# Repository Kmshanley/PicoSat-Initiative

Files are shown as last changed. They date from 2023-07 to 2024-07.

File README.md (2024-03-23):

# PicoSat-Initiative
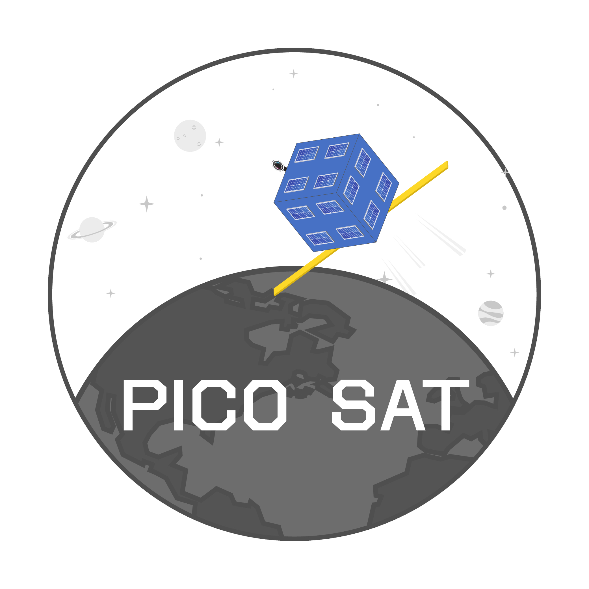
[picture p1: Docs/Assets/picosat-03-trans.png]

The Wentworth Picosat initiative is a group at Wentworth Institute of technology dedicated to making a pocket cube satellite capable of earth observation from LEO.

The pocket cube standard requires satellites to be 5x5x5cm and under 250 grams. Upon completion of this Wentworth PicoSat it will become one of the smallest satellites capable of high resolution imagery from LEO.

* **Homepage:** <https://picosat.notion.site>
* **Communication:** <https://discord.gg/C9kFq642a>

Organization
------------------------
This repository is divided into two primary sections:
### Test
> Contains all firmware related to testing boards or individual components.
### Flight
> Contains the development for the main flight firmware that will be deployed in space.

Getting Started
------------------------
The easiest way to get started is by using the Stm32CubeIDE.

Downloadable here: https://www.st.com/en/development-tools/stm32cubeide.html

From here you should be able to import the various project files (.ioc) and CubeIDE will handle setup, build tools, and compilation.

High Level Overview
------------------------
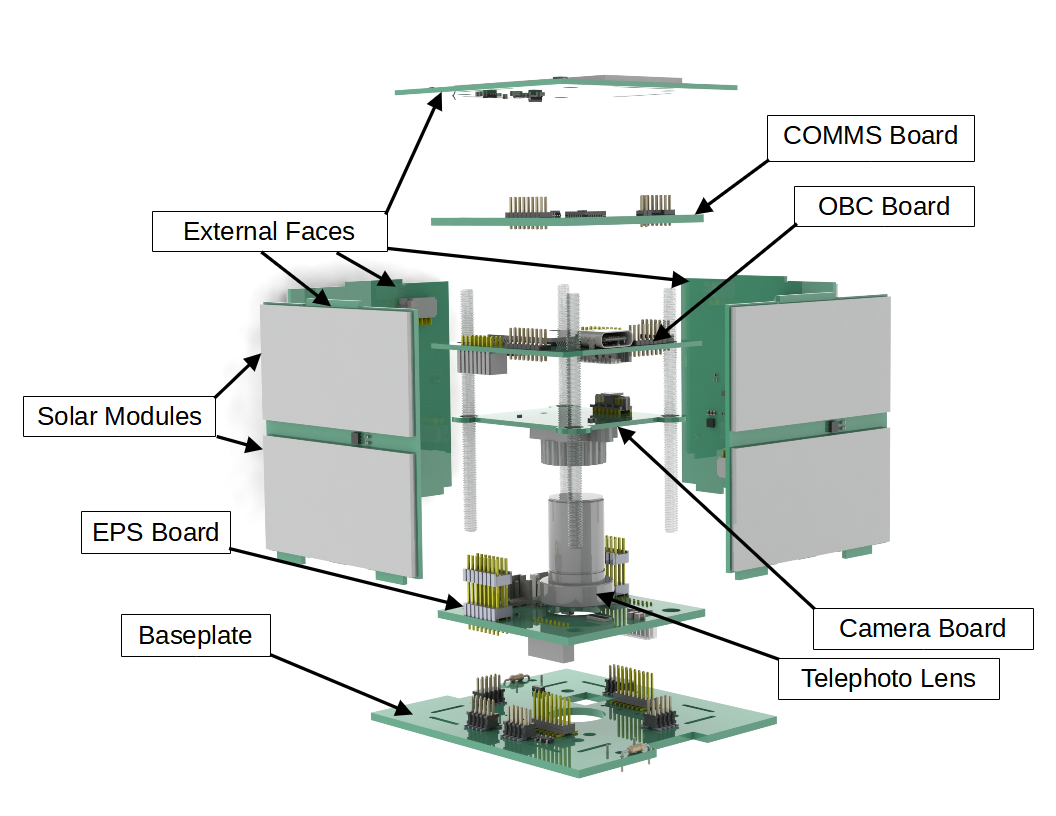
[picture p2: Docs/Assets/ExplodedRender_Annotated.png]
Exploded and Annotated Render of the Satellite's Internal Stack


The Satellite is composed of several **subsystems**:

* Onboard Computer System (OBC)
    * Responsible for handling commands from the ground station
    * Running ADCS algorithms
    * Commanding the image sensor to take pictures
        * Compressing and Storing these pictures until downlink
    * Gathering telemetry from sensors
        * Feeding telemetry to the appropriate subsystem
            * I.e. LUX sensor data to ADCS
    * Managing Satellite Energy consumption
        * Monitoring battery health and determining wakeup periods
* Electrical Power System (EPS)
    * Responsible for generating, storing, and regulating electrical power
* Communications (COMMS)
    * Responsible for uplink and downlink to ground station 
* Attitude Control and determination (ADCS)
    * Responsible for determining the attitude (rotation) of the satellite
    * Responsible for executing rotational maneuvers

Hardware Overview
------------------------
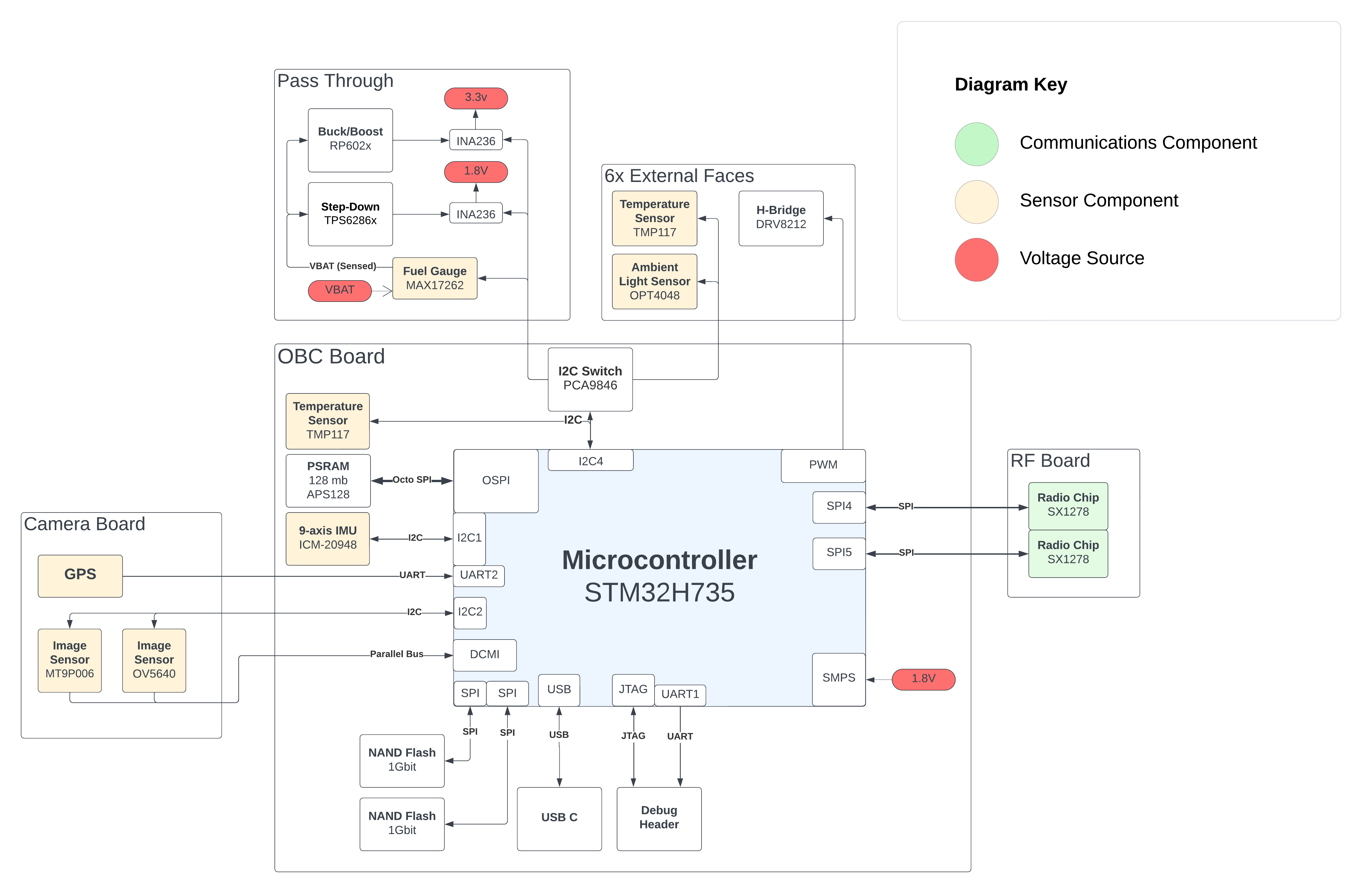
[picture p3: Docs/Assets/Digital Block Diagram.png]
System diagram of all satellite components


Contact
------------------------
You can join our discord with the link above or contact us directly via email:

OBC Team Lead (Kieran Shanley): <kmshanley01@gmail.com>

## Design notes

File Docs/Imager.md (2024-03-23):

# Imager

The Satellite's primary goal is to capture high resolution photos of the surface of the earth.

In order to accomplish this, the satellite is equipped with two cameras.

1. OV5640 image sensor (Wide angle camera)
    * Connected to the camera board via ribbon cable
    * 5 MP (2592 H x 1944 V)
    * 250 m/pix GSD
    * 67 degree FOV
    * Optical Format 1/4"
2. MT9P006 image sensor (telephoto)
    * Directedly soldered to camera board
    * 5 MP (2592 H x 1944 V)
    * 50 m/pix GSD
    * 12 degree FOV
    * Optical Format 1/2.5"

Both cameras have a I/O line dedicated to shutting down the sensor. These two lines will allow us have the image sensors share data busses; by only having one sensors active at a time. Each sensor is connected to two data busses: DCMI (parallel) and I2C. The I2C bus is used to command and configure the sensor. The DCMI bus is used to transfer image data.

The DCMI bus is accessible via a DMA (direct memory access) master. This allows data to be transferred out of the DCMI bus hardware to a memory location without using the CPU.

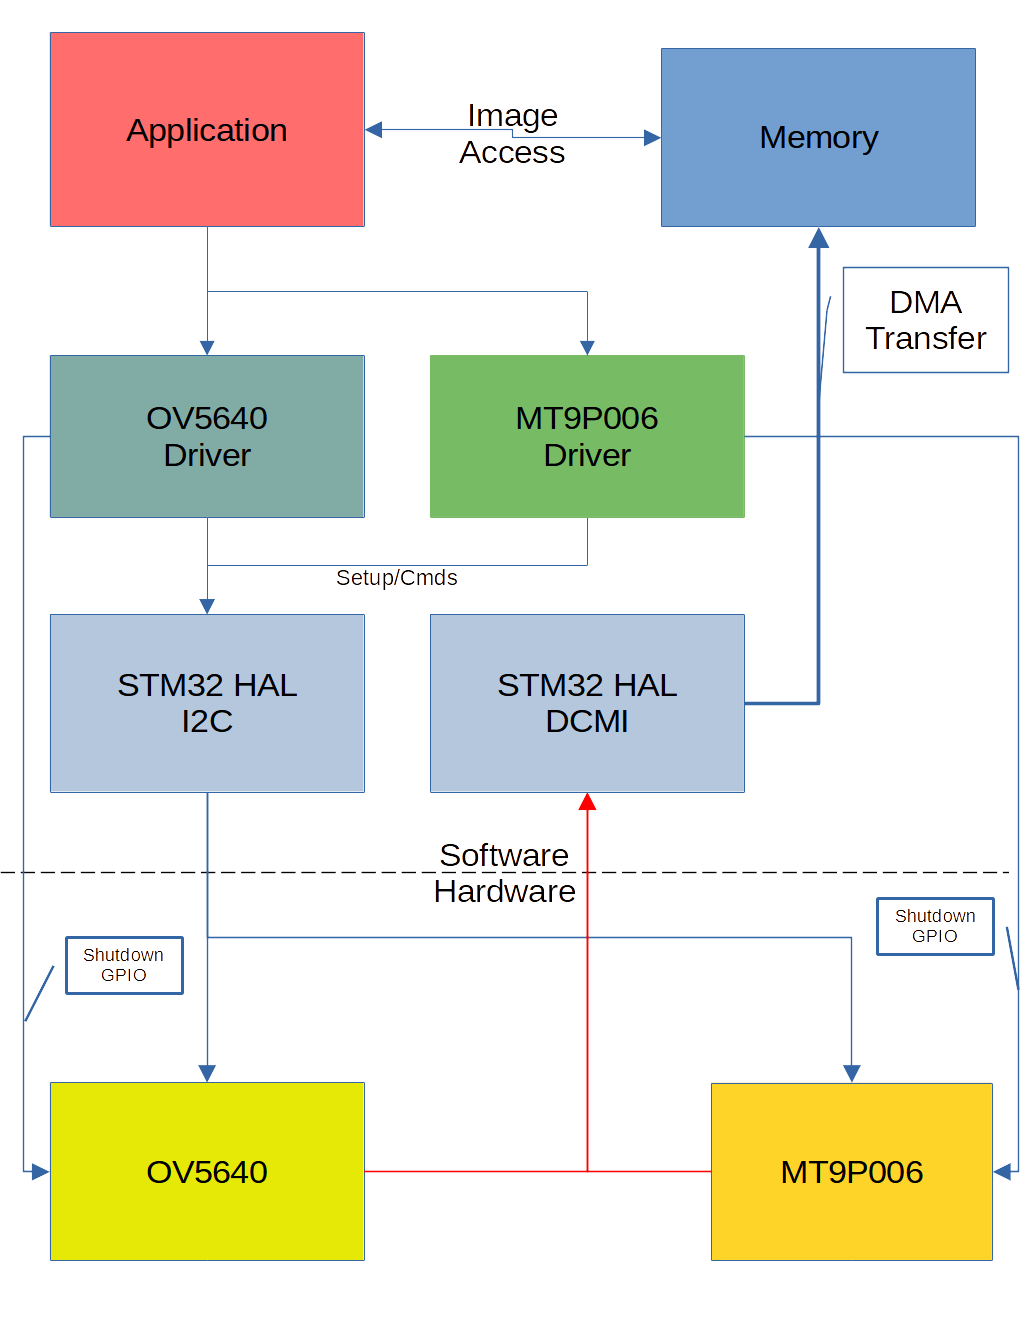
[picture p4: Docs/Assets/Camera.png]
Diagram of the Camera Software Architecture


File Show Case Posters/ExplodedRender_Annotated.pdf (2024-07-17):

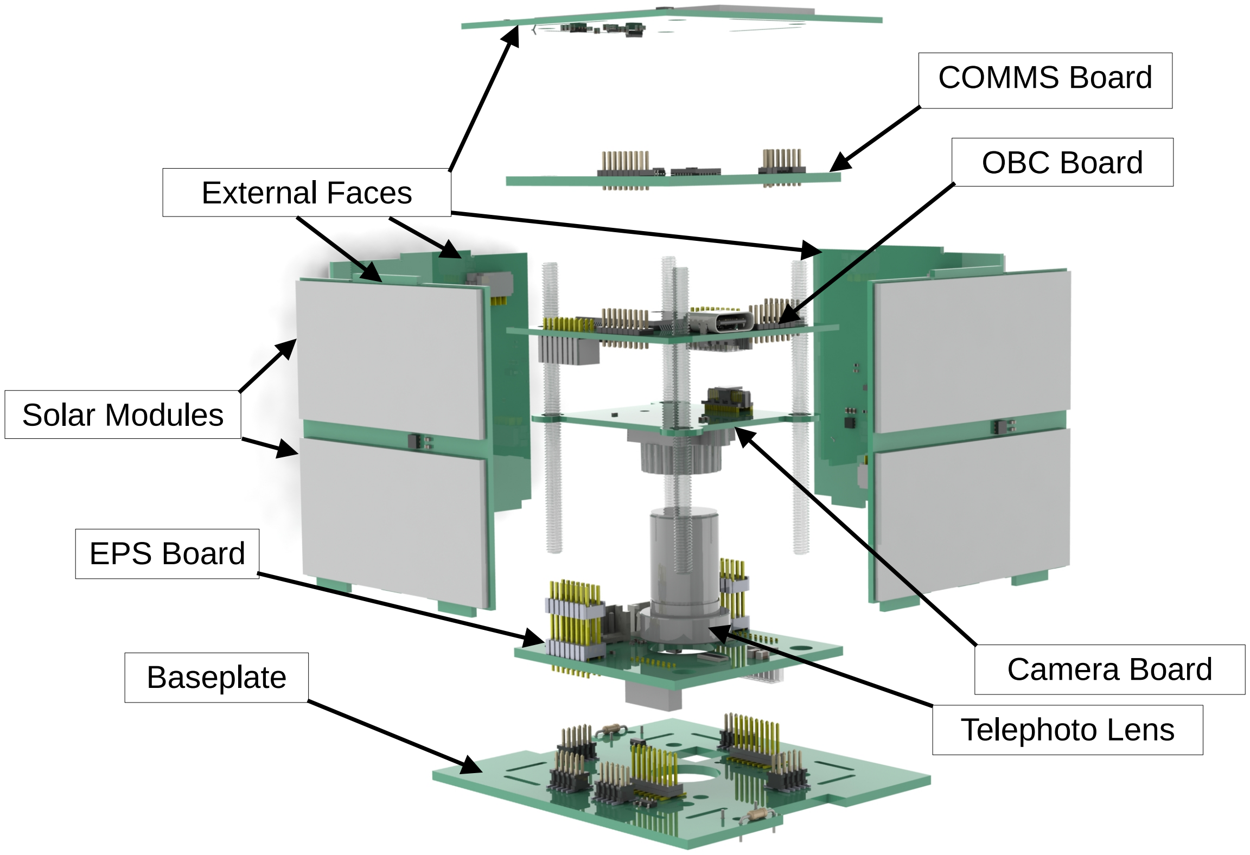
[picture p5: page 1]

COMMS Board

OBC Board

Camera Board

EPS Board

Baseplate
Telephoto Lens

External Faces

Solar Modules

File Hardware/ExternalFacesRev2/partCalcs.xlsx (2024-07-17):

SPV1040 Inductor
Vout | 4.2
Vmpp | 3.35
Pmax (mW) | 368
Duty Cycle | 0.2023809524
Switching Frequency | 100000 |  |  | 1.5e-08
CM mode inductance | 6.245267865e-09 |  | 30% | -30%
Lx | 9.91873805e-06 |  | 1.95e-08 | 1.05e-08
9e-06
Voc | 4.15
Imax | 0.1172
Output voltage partitioning
Vout Max | 4.2
Resistor ratio | 2.3600
 | R1 | R2
Slected Resistors | 1000000 | 420000
Vout Real | 4.226190476

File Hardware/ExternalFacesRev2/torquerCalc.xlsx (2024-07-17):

Total Resistance | Coil Resistance (Ohms) | Area Sum (m^2) | Number of Coils | Voltage | Amps | Magnetic Dipole (A-m^2) | Watts | Watt per dipole | Lat | Long | Altitude (km) | Description | North Comp (nT) | East/West Comp (nT) | Vertical Comp (nT) | Total |  | Roll (N * m) | Pitch (N * m) | Yaw (N * m) | Roll (rad/s^2) | Pitch (rad/s^2) | Yaw (rad/s^2) | Roll (deg /s^2) | Pitch (deg /s^2) | Yaw (deg /s^2)
150 | 75 | 0.1356 | 2 | 3.7 | 0.02466666667 | 0.0033448 | 0.09126666667 | 27.28613569 | 42° 21' 31" N | 71° 3' 24" W | 700 | LEO over bosto | 1.44234e-05 | -3.1452e-06 | 3.39189e-05 | 3.69914e-05 | 0 | -5.460501954e-07 | 0 | 2.321979896e-07 | -0.005242081876 | 0 | 0.0022291007 | -0.3003491673 | 0 | 0.1277180622
100 | 50 | 0.145 | 2 | 3.7 | 0.037 | 0.005365 | 0.1369 | 25.51724138 |  | Dipole vector: |  |  | 0 | 0.0160987 | 0 |  | 1e-09
100 | 50 | 0.145 | 2 | 10 | 0.1 | 0.0145 | 1 | 68.96551724
100 | 25 | 0.29 | 4 | 3.7 | 0.037 | 0.01073 | 0.1369 | 12.75862069 |  |  |  |  |  |  |  |  | Mass of Sat
100 | 16.66666667 | 0.4351 | 6 | 3.7 | 0.037 | 0.0160987 | 0.1369 | 8.503792232 |  |  |  |  |  |  |  |  | 0.25
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

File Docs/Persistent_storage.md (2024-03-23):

# Persistent Storage

OBC flight is equipped with 2x 1Gbit W25N01GW Winbond QSPI NAND flash chips.
These chips are 1Gbit, or 128M-byte in size. They are connected to the STM32H7 primary microcontroller via QSPI.
However, from the perspective of the STM32H7 these two chips are connected to a OCTOSPI interface, which is then split into two QSPI interfaces.

One issue with these NAND chips is that they have a 128K-Byte block size. Which means that the **minimum** amount of data that can be erased in one operation is 128K-bytes. NAND flash may also ship with *bad blocks* (blocks that cannot be read from or written to), or develop them in there lifespan. NAND flash also experiences significant wear on writes/erases (W25N01 is rated for 10,000 cycles), necessitating the use of special data organization to ensure *wear leveling*.

Luckily, there are filesystems designed for this exact application.
The filesystem we chose for our satellite is **YAFFS** (<https://yaffs.net/>).
YAFFS is designed to directly interact with and handle NAND flash. This will allow us to abstract away complex NAND file handing and be able to simply access files from a *POSIX-like interface*. 

Yaffs also supplies a special wrapped for RTOS's, called *Yaffs Direct Interface*. We will be using this wrapped to integrate YAFFS with FREERTOS.

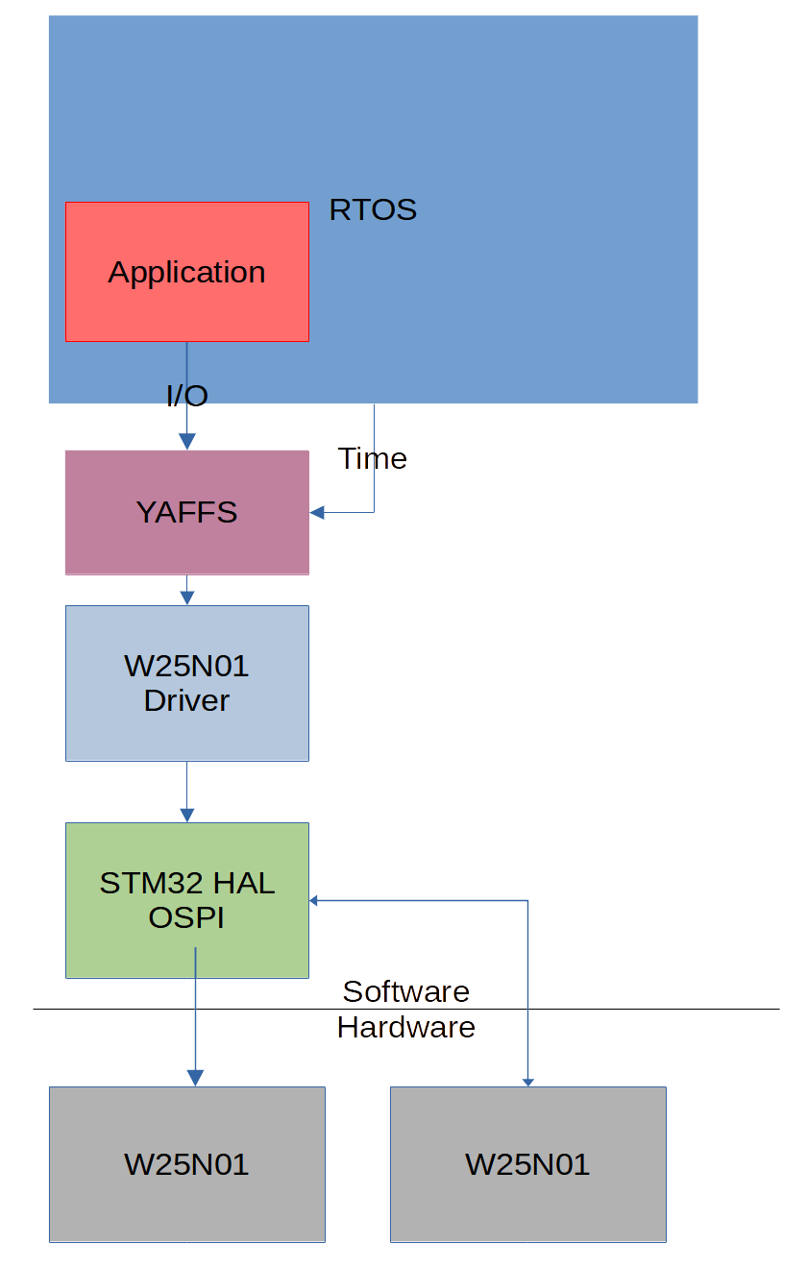
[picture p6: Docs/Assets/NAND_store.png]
Diagram of the Storage software Architecture


# Usage
* Pictures
* Ephemeris Data
* Logging
    * A max file size will be allocated
        * Once this size is reached, the oldest logs will be overwritten
* Firmware images 
    * Images uploaded from the ground station will first be loaded into NAND

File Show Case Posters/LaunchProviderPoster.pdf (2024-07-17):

# How to get to LEO: Launch Provider

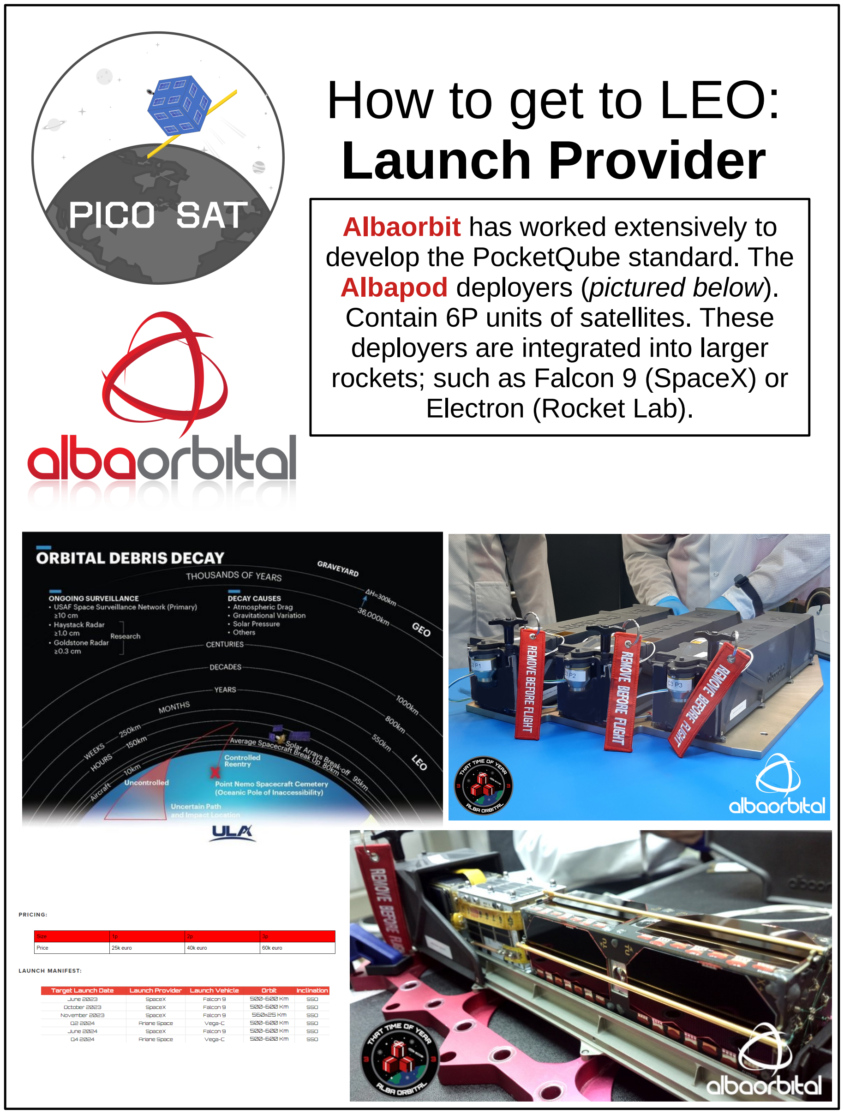
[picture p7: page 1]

Albaorbit has worked extensively to develop the PocketQube standard. The Albapod deployers (pictured below). Contain 6P units of satellites. These deployers are integrated into larger rockets; such as Falcon 9 (SpaceX) or Electron (Rocket Lab).

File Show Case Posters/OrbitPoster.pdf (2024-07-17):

# Destination: Low Earth Sun

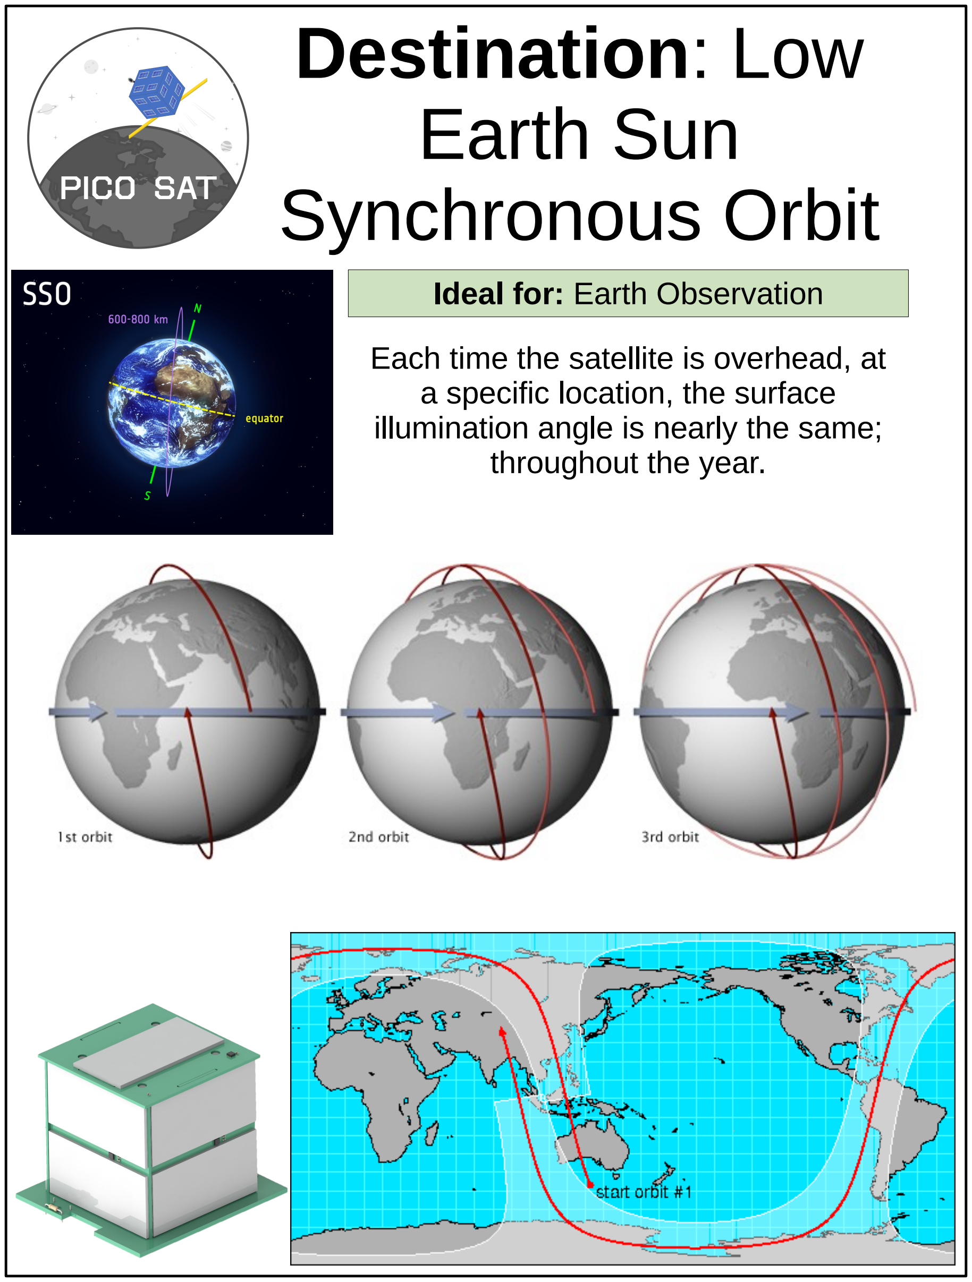
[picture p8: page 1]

# Synchronous Orbit

Each time the satellite is overhead, at a specific location, the surface illumination angle is nearly the same; throughout the year.

Ideal for: Earth Observation

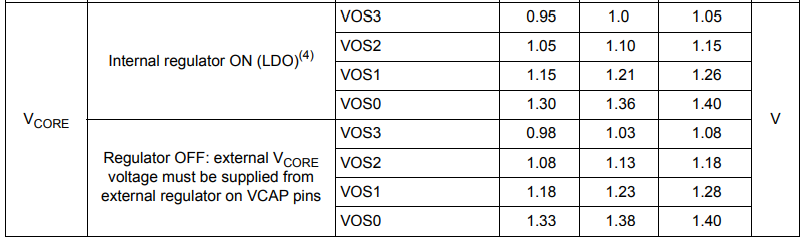
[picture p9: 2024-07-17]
Hardware/OBC-Flight_Rev0/VcoreSupplyOpCond.PNG

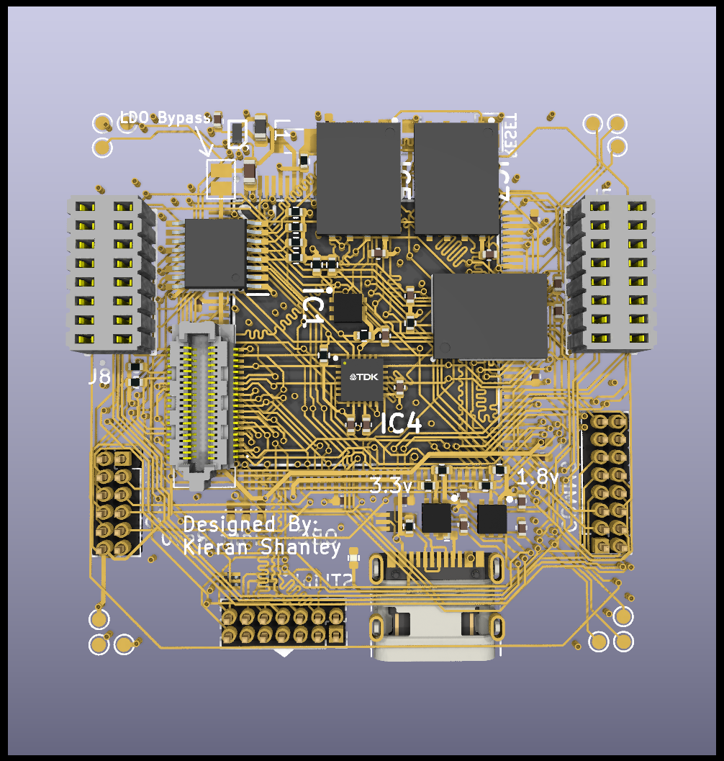
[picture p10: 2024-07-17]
Hardware/OBC-Flight_Rev0/OBC-Flight_SeeThroughBack.png

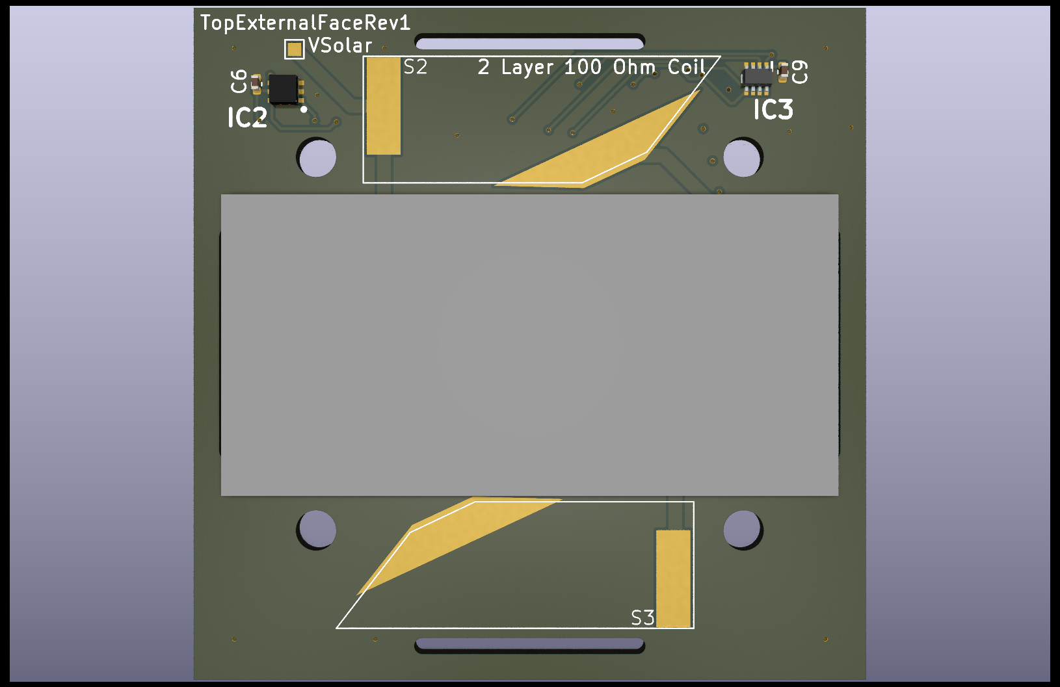
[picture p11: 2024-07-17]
Hardware/TopExternalFaceRev1/TopExternalFaceRev1_Top.png

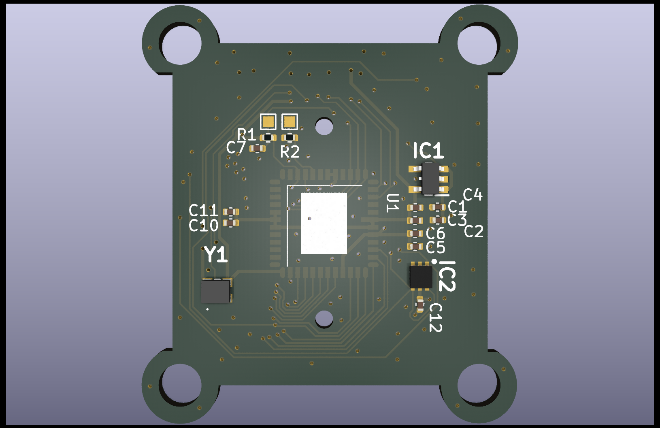
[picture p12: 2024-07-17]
Hardware/CameraBoard_Rev0/CameraBoard_Bottom.png

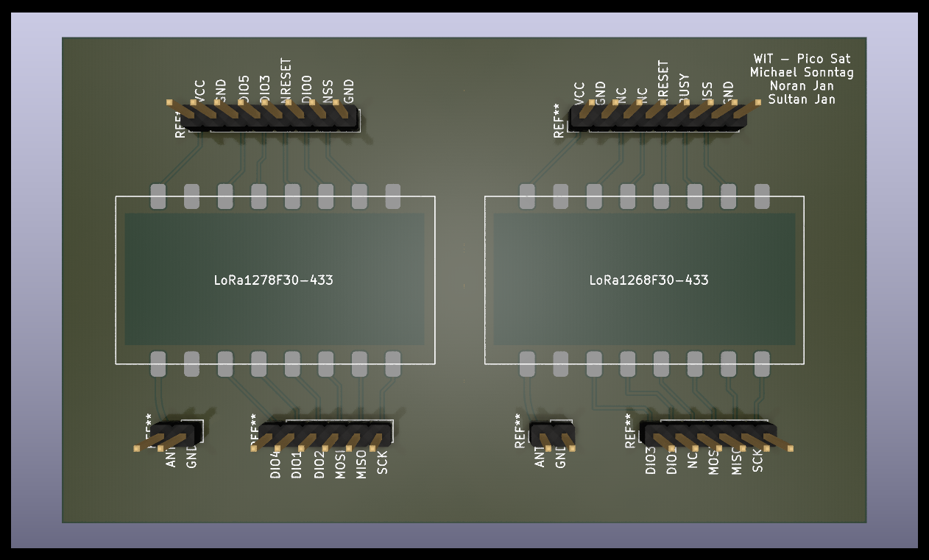
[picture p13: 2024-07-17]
Hardware/G-NiceRF Breakout Board/G-NiceRF Breakout Board.png

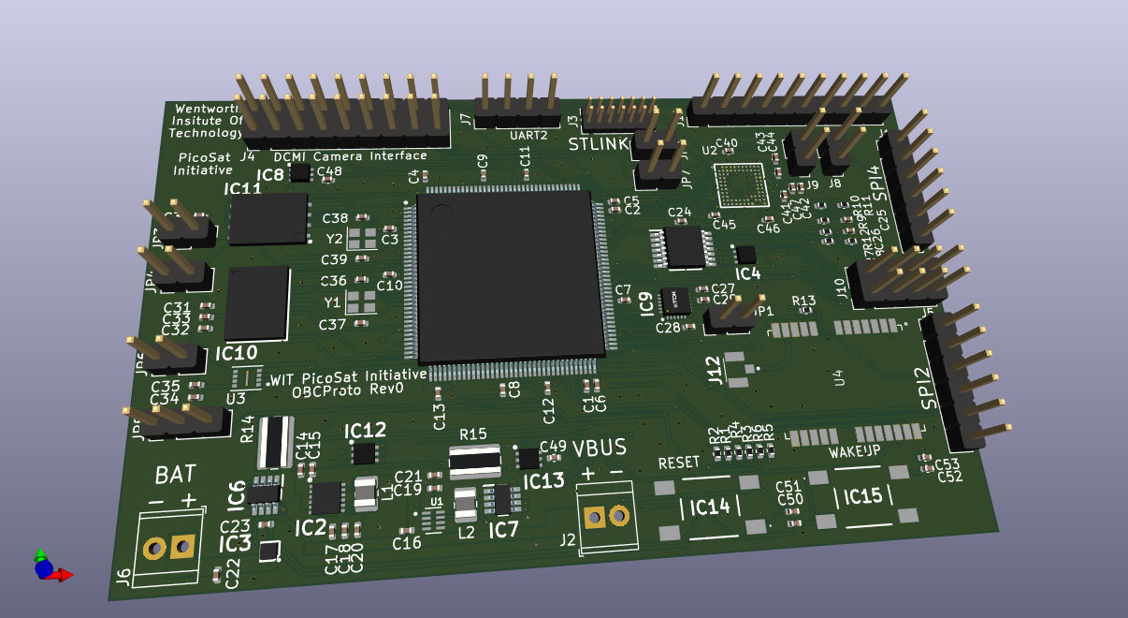
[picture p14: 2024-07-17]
Hardware/OBCProto/OBCProto.png

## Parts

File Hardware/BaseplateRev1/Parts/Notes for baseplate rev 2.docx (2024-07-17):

Re route everything

Move caps away from screw hole

Route rf signal to both poles of dipole

Pick and implement different transistors

Move kill switches back to appropriate position and make them even

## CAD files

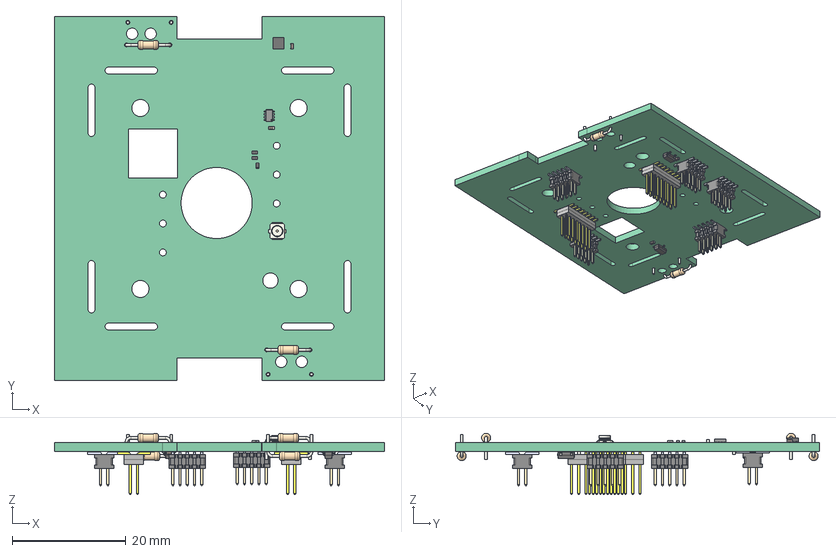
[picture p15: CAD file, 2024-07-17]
Hardware/BaseplateRev1/BaseplateRev1.step
58.0 x 64.0 x 10.8 mm
Pcb_3d0
REFinduc_R_0402_1005Metric_394f7394ac2b x 3
R1_R_Axial_DIN0204_L36mm_D16mm_P762mm_Horizontal_5bcf6e7bee84 x 4
C1_C_0402_1005Metric_3298216d9a1e x 4
J8_U.FL_Hirose_U.FL-R-SMT-1_Vertical_2761da9aecd1
PinsArrayL
PinsArrayL001
PinsArrayL002
PinsArrayL003
PinsArrayR
PinsArrayR001
PinsArrayR002
PinsArrayR003
BODY-SON
FTSH-105-01-L-DV
FTSH-105-01-L-DV001
FTSH-105-01-L-DV002
FTSH-105-01-L-DV003
FTSH-105-01-L-DV004
FTSH-105-01-L-DV005
FTSH-105-01-L-DV006
FTSH-105-01-L-DV007
FTSH-105-01-L-DV008
FTSH-105-01-L-DV009
FTSH-105-01-L-DV010
FTSH-105-01-L-DV011
FTSH-105-01-L-DV012
FTSH-105-01-L-DV013
FTSH-105-01-L-DV014
FTSH-105-01-L-DV015
FTSH-105-01-L-DV016
FTSH-105-01-L-DV017
FTSH-105-01-L-DV018
FTSH-105-01-L-DV019
FTSH-105-01-L-DV020
Q2_SOT_23_65e23e147aa5 x 2
FTSH-105-01-L-DV021 x 4
FTSH-105-01-L-DV022 x 4
FTSH-105-01-L-DV023 x 4
FTSH-105-01-L-DV024 x 4
FTSH-105-01-L-DV025 x 4
FTSH-105-01-L-DV026 x 4
FTSH-105-01-L-DV027 x 4
FTSH-105-01-L-DV028 x 4
FTSH-105-01-L-DV029 x 4
FTSH-105-01-L-DV030 x 4
FTSH-105-01-L-DV031 x 4
FTSH-105-01-L-DV032 x 4
FTSH-105-01-L-DV033 x 4
FTSH-105-01-L-DV034 x 4
FTSH-105-01-L-DV035 x 4
FTSH-105-01-L-DV036 x 4
FTSH-105-01-L-DV037 x 4
FTSH-105-01-L-DV038 x 4
FTSH-105-01-L-DV039 x 4
FTSH-105-01-L-DV040 x 4
FTSH-105-01-L-DV041 x 4
FW-08-03-G-D-085-210_top_body x 2
FW-08-03-G-D-085-210_pins2 x 2
FW-08-03-G-D-085-210_pins1 x 2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

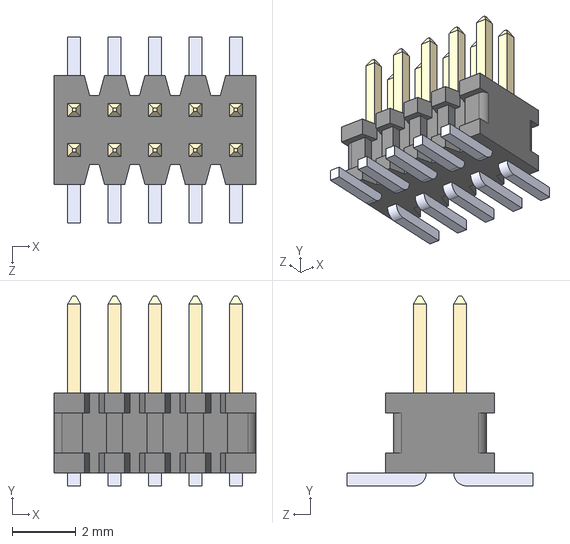
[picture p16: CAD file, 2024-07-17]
Hardware/BaseplateRev1/Parts/FTSH-105-01-L-DV/FTSH-105-01-L-DV--3DModel-STEP-56544.STEP
6.35 x 5.97 x 5.84 mm

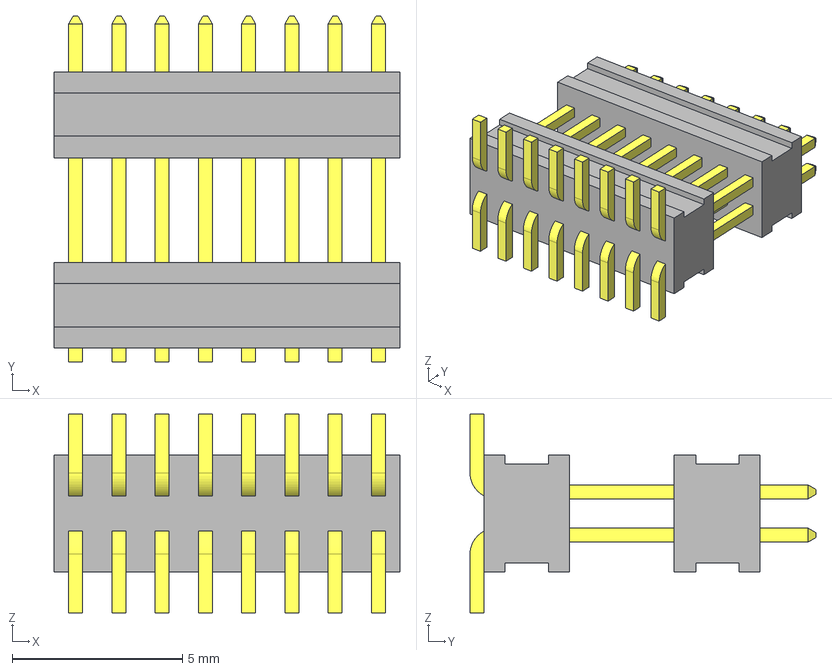
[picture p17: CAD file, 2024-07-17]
Hardware/BaseplateRev1/Parts/FW-08-03-G-D-335-065.stp
10.2 x 10.2 x 5.84 mm
FW-08-03-G-D-335-065_top_body
FW-08-03-G-D-335-065_pins2
FW-08-03-G-D-335-065_pins1
FW-08-03-G-D-335-065_bottom_body

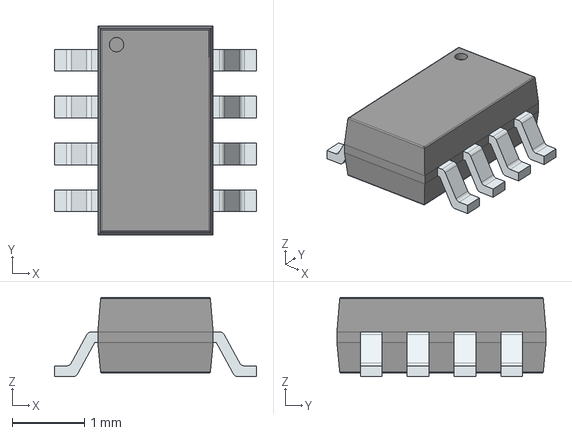
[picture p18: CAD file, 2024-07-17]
Hardware/BaseplateRev1/Parts/INA236AIDDFR/INA236AIDDFR.stp
2.80 x 2.90 x 1.10 mm
PinsArrayLR

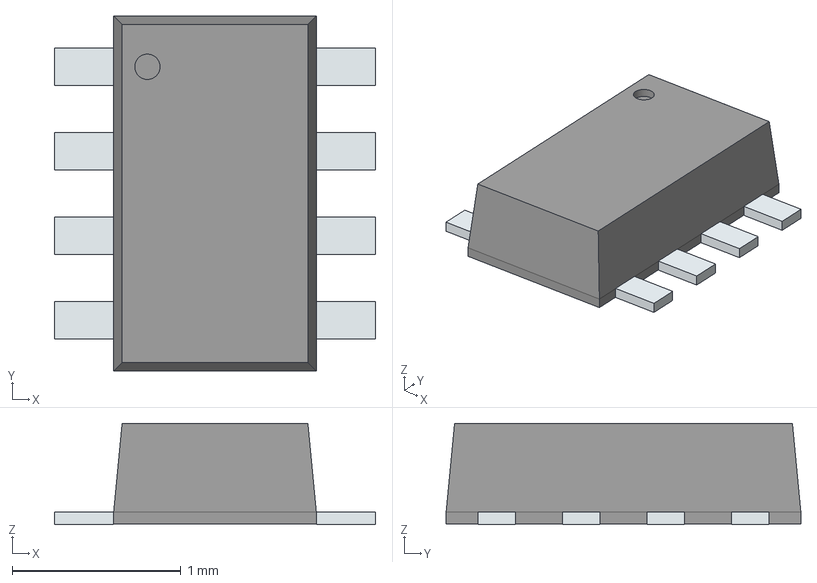
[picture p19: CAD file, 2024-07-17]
Hardware/BaseplateRev1/Parts/OPT4048DTSR/OPT4048DTSR.stp
1.90 x 2.10 x 0.598 mm
PinsArrayL
PinsArrayR

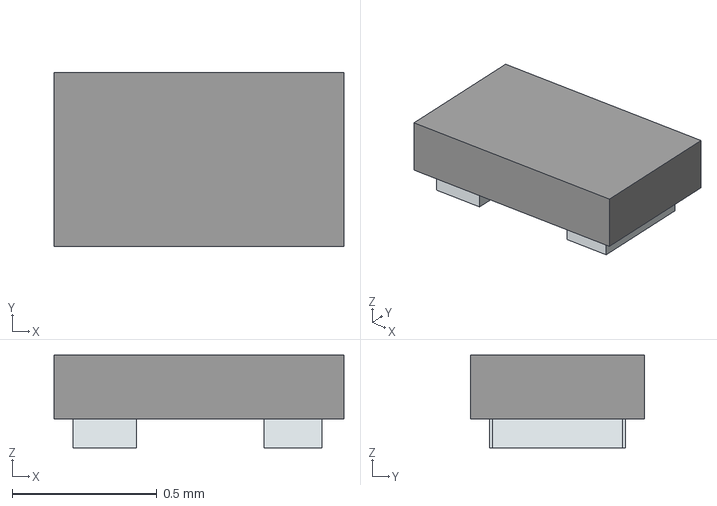
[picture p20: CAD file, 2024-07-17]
Hardware/BaseplateRev1/Parts/PMCB60XNEZ/PMCB60XNEZ.stp
1.00 x 0.6 x 0.32 mm
Pins

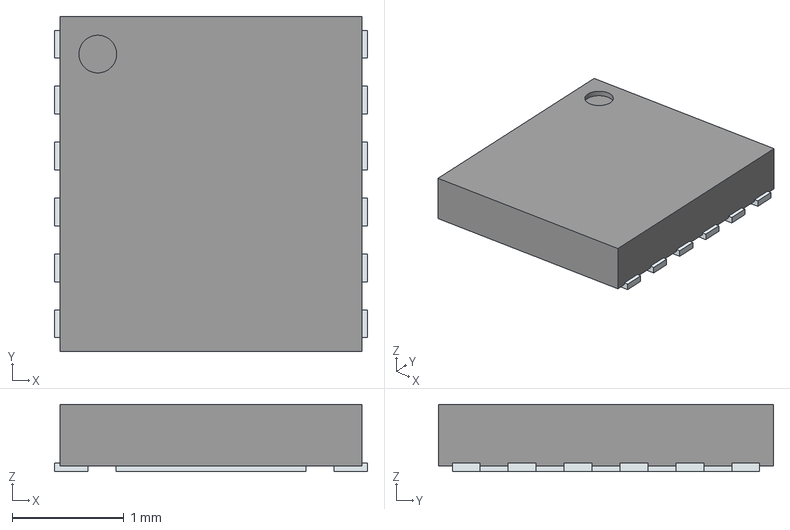
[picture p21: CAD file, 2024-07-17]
Hardware/BaseplateRev1/Parts/RP604K331A-TR/RP604K331A-TR.stp
2.80 x 3.00 x 0.6 mm
ThermalPin
PinsArrayLR

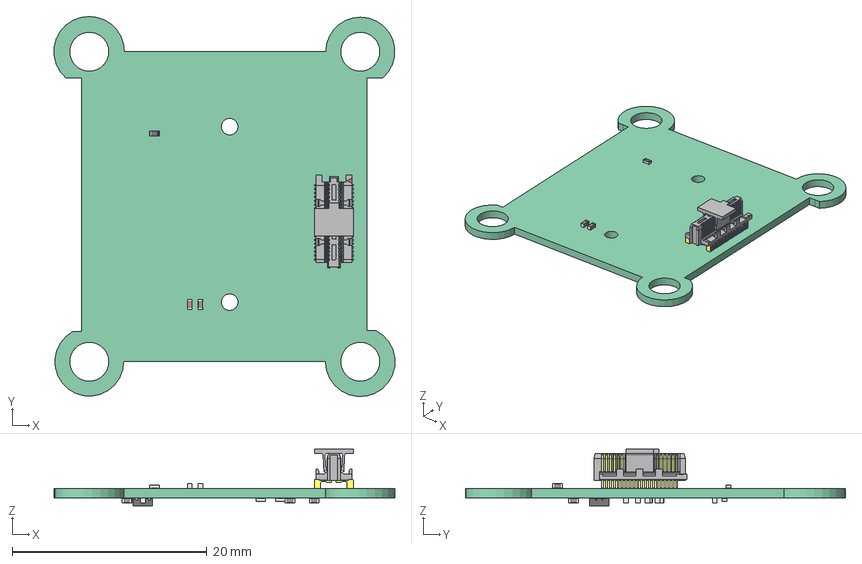
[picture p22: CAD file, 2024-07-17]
Hardware/CameraBoard_Rev0/CameraBoardRev0_D.step
35.0 x 39.0 x 5.83 mm
Pcb_b3c2
C9_C_0402_1005Metric_ee4f209181d8 x 12
R3_R_0402_1005Metric_565fab136afc x 3
ST4-20-1.50-L-D_pin
ST4-20-1.50-L-D-P-TR_terminal
BODY-SON

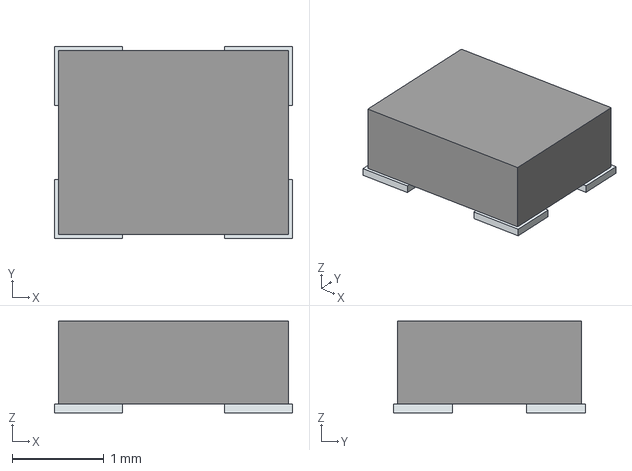
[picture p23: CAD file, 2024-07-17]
Hardware/CameraBoard_Rev0/Parts/ECS-2520MV-480-CM-TR/ECS-2520MV-480-CM-TR.stp
2.59 x 2.09 x 1.00 mm
Pins

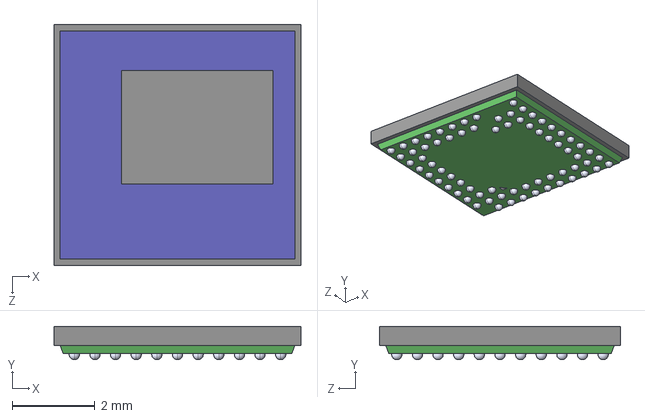
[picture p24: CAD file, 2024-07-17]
Hardware/CameraBoard_Rev0/Parts/OV5640-A71A/OV5640-A71A.step
5.99 x 0.81 x 5.83 mm

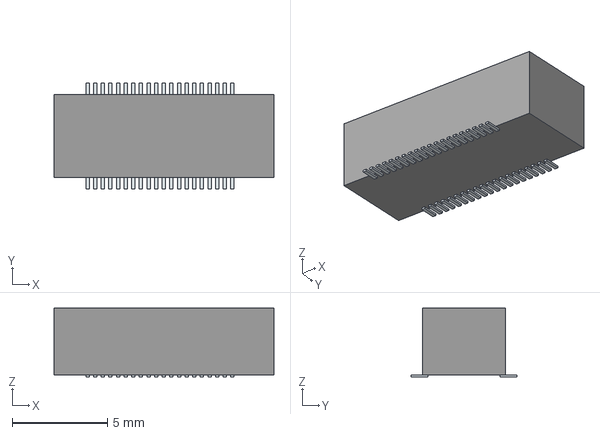
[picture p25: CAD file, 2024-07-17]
Hardware/CameraBoard_Rev0/Parts/SS4-20-3.00-L-D-K-TR/SS4-20-3.00-L-D-K-TR.stp
11.5 x 5.55 x 3.60 mm
Pins

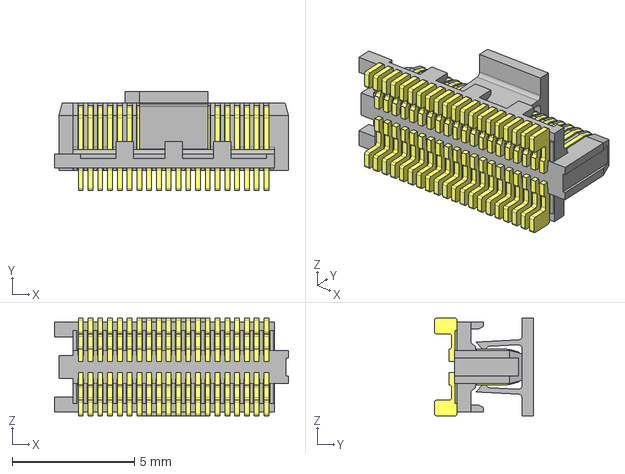
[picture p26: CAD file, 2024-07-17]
Hardware/CameraBoard_Rev0/Parts/ST4-20-1.50-L-D-P-TR/ST4-20-1.50-L-D-P-TR.step
9.58 x 4.05 x 4.00 mm
ST4-20-1.50-L-D_pin
ST4-20-1.50-L-D-P-TR_terminal

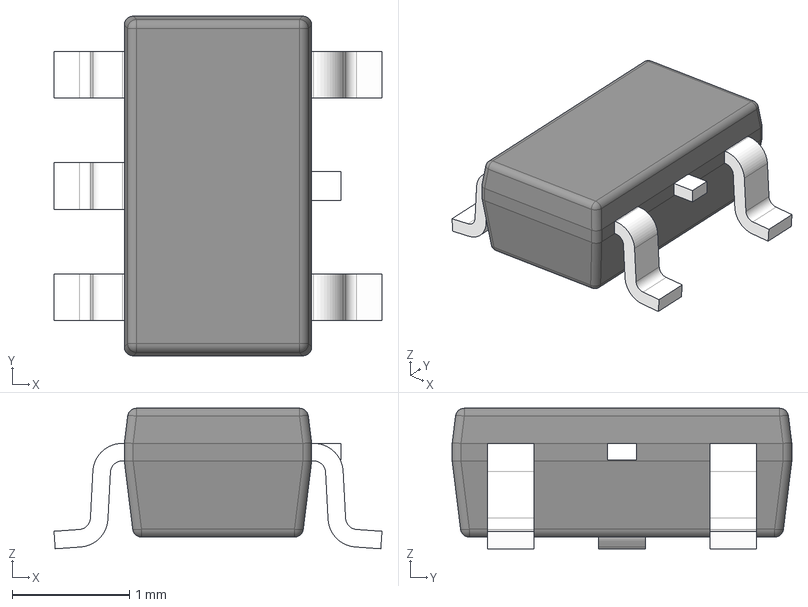
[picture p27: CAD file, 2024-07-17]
Hardware/CameraBoard_Rev0/Parts/TPS7A0228PDBVR/TPS7A0228PDBVR.stp
2.80 x 2.90 x 1.20 mm
BODY-SOT
LEAD-SOT x 5
LEAD-DUMMY

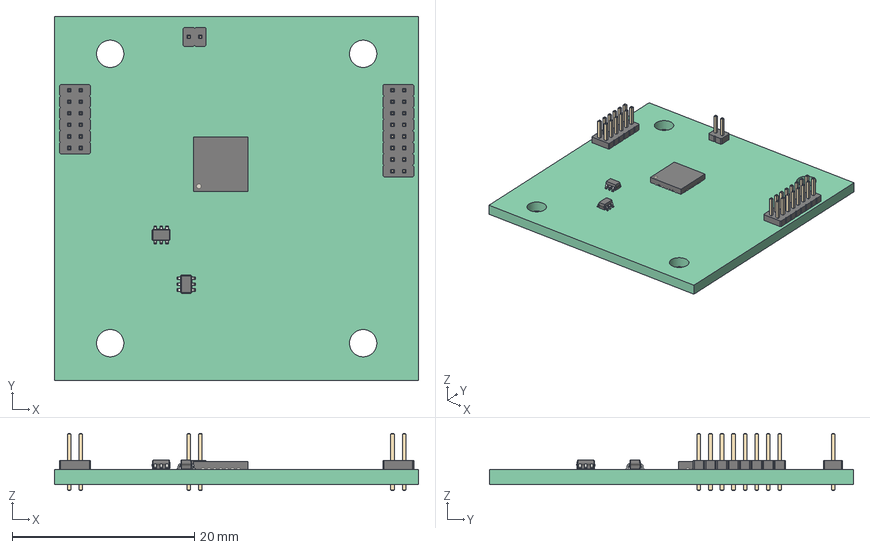
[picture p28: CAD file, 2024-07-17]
Hardware/Comms board - Version1.0/CommsRev0.step
40.0 x 40.0 x 6.30 mm
Pcb_e19c
J4_PinHeader_2x08_P127mm_Vertical_4db083f2690b
J3_PinHeader_2x06_P127mm_Vertical_37d54021ef1c
J2_PinHeader_1x02_P127mm_Vertical_719ac9e5078b
U1_SOT_363_SC_70_6_38a6dca92cb8 x 2
U4_QFN_28_1EP_6x6mm_P065mm_EP48x48mm_13f4ae8375c3

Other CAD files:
Hardware/ExternalFacesRev2/Parts/DRV8212PDSGR/DRV8212PDSGR.stp
Hardware/ExternalFacesRev2/Parts/KXOB121K04TF/SM141K06TFV.STEP
Hardware/BaseplateRev0/FTSH-105-XX-X-DV.step.SLDASM
Hardware/BaseplateRev0/INA236AIDDFR.step.SLDASM
Hardware/BaseplateRev0/L_1008_2520Metric.step.SLDASM
Hardware/BaseplateRev0/Parts/TPS62840DLCR/TPS62840DLCR.step
Hardware/BaseplateRev0/RP604K331A-TR.step.SLDASM
Hardware/BaseplateRev0/R_1020_2550Metric.step.SLDASM
Hardware/BaseplateRev0/R_Axial_DIN0204_L3.6mm_D1.6mm_P7.62mm_Horizontal.step.SLDASM
Hardware/BaseplateRev0/SOLID-2.step.SLDPRT
Hardware/BaseplateRev0/SOLID-6.step.SLDPRT
Hardware/BaseplateRev0/baseplate PCB.step.SLDPRT
Hardware/BaseplateRev0/stencilHolder_baseplateRev0.SLDPRT
Hardware/BaseplateRev0/stencilHolder_baseplateRev0.STL
Hardware/BaseplateRev1/BaseplateRev1-B_Silkscreen.dxf
Hardware/BaseplateRev1/BaseplateRev1-F_Silkscreen.dxf
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

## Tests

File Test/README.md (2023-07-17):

# Current Test Firmware

### devBoardTest
------------------------
Designed to test every component on the OBC-Proto board. Will conduct test I/O operations on external memory and poll every sensor on board. A successful pass on this program will validate that a OBC proto board has been manufactured correctly.
### picoSat_cameraTest
------------------------
Designed to test the use of a OV5640 camera module with a NUCLEO-H723ZG development board. This program will validate that the DCMI interface of the stm32h723 works with a OV5640
### picoSat_epsTest
------------------------
Designed to test all the digital sensors present on the EPS board. This program will validate that a EPS board has been manufactured correctly (or at least all the digital sensors).

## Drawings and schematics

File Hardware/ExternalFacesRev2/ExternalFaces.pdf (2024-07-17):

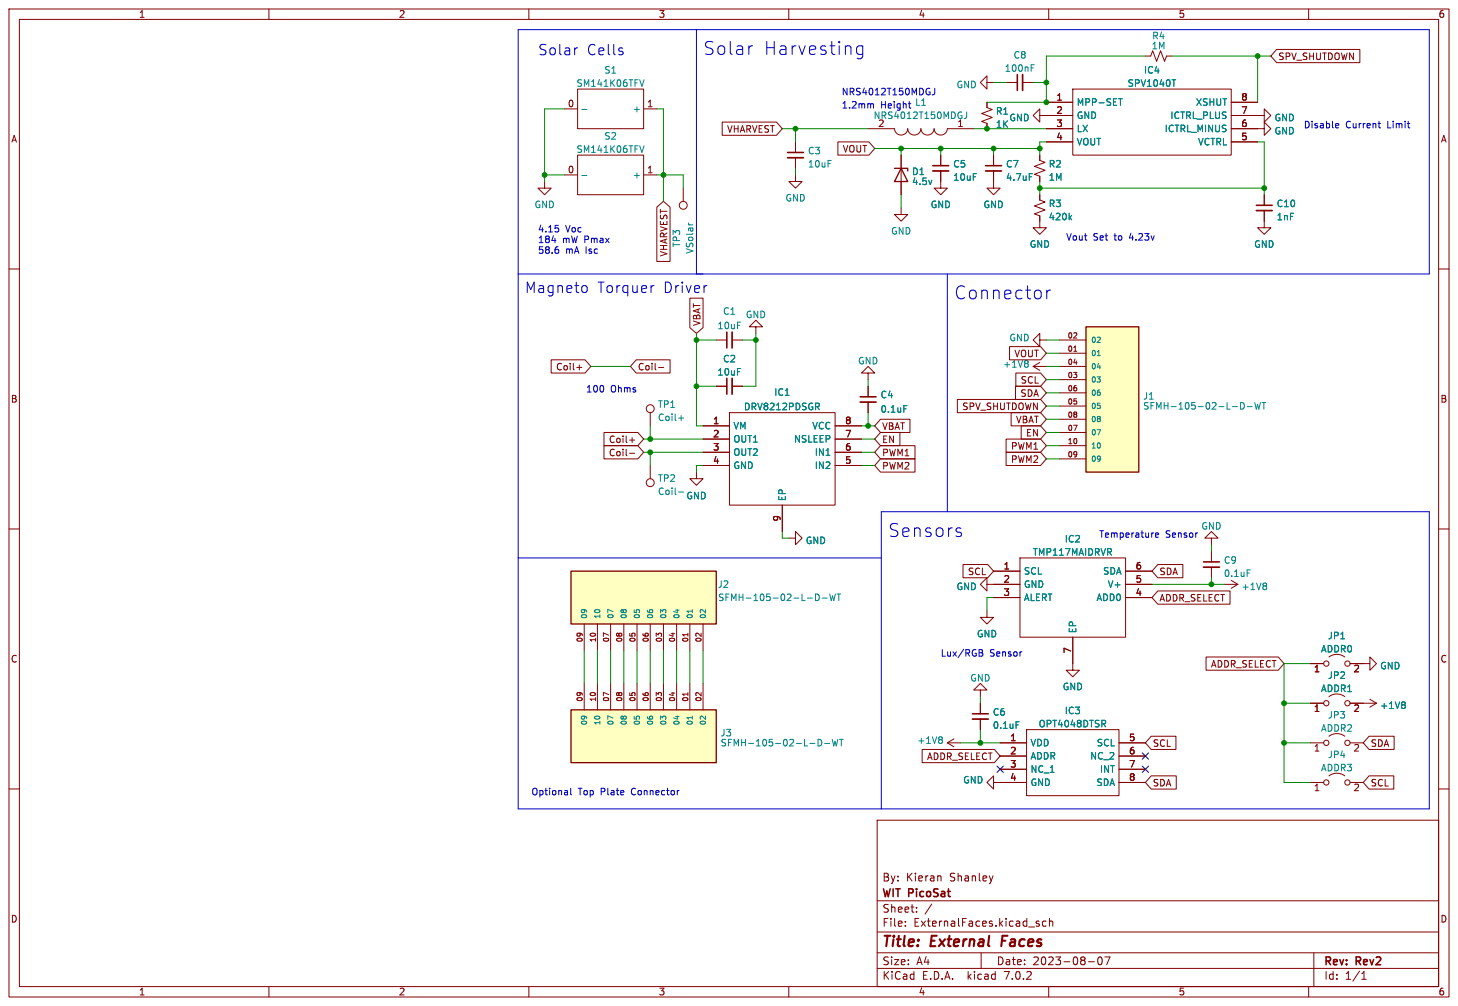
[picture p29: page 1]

4.15 Voc 184 mW Pmax 58.6 mA Isc Solar Cells

Id: 1/1 Title: External Faces

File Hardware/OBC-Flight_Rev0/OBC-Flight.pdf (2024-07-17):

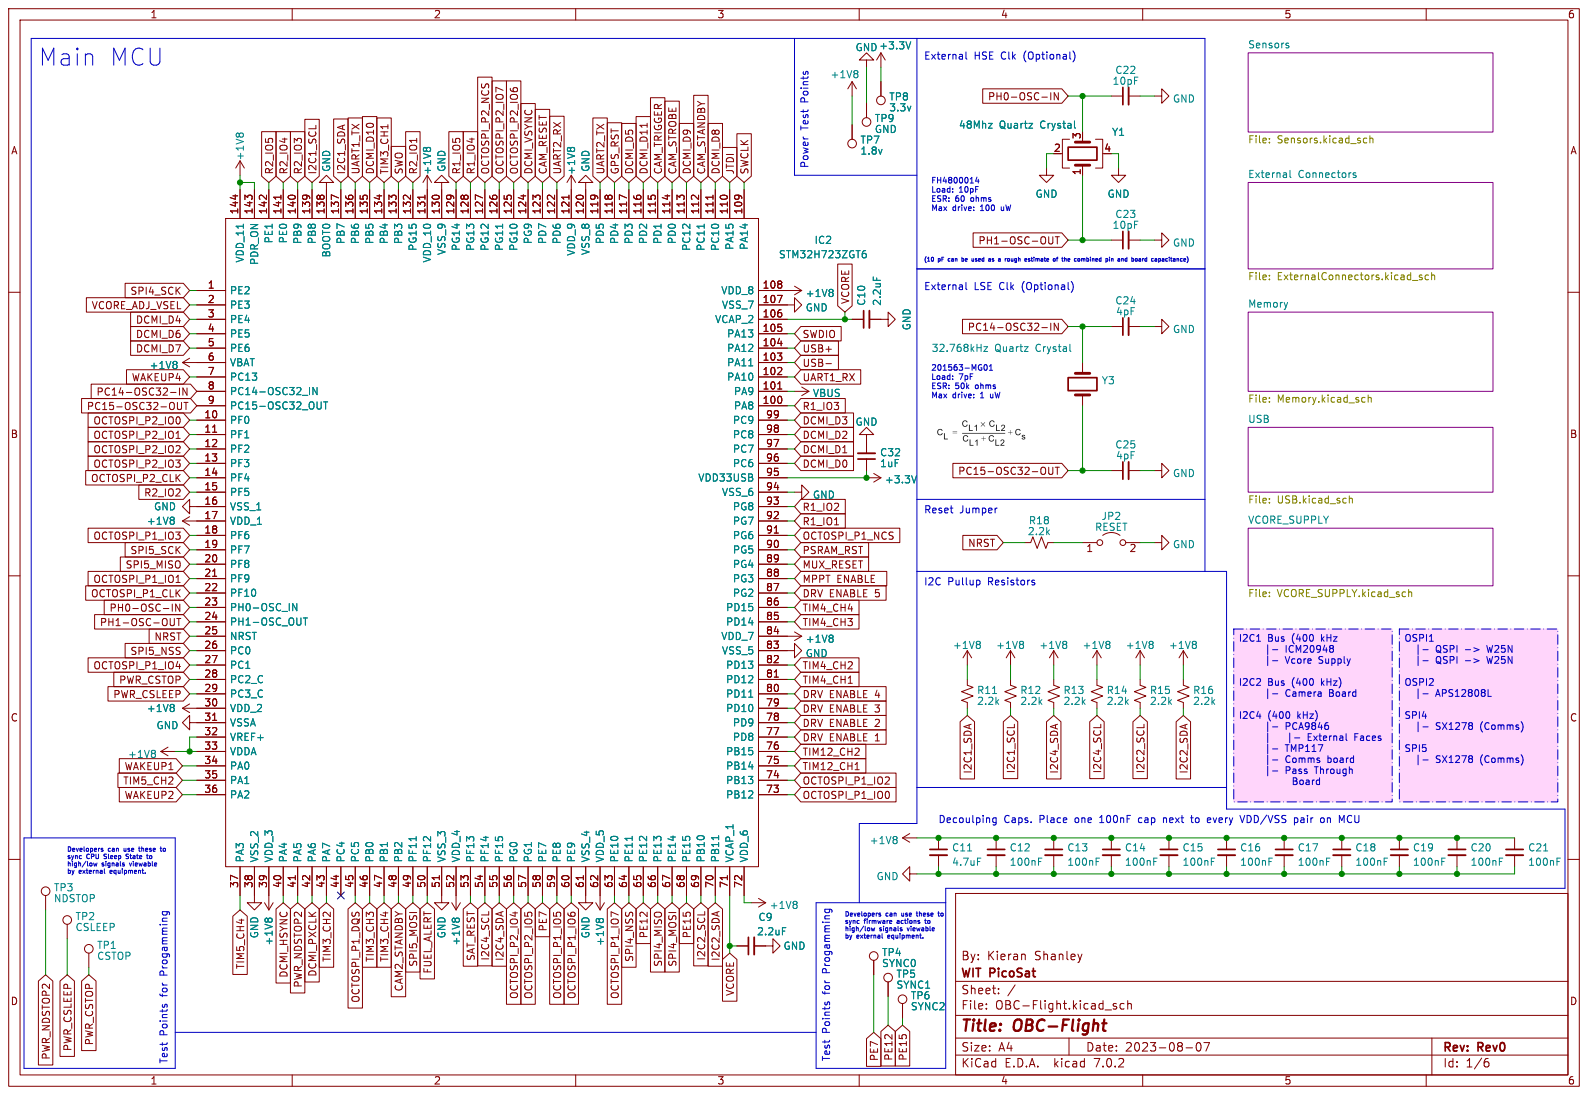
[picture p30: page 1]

Sensors File: Sensors.kicad_sch VCORE_SUPPLY
File: VCORE_SUPPLY.kicad_sch External Connectors File: ExternalConnectors.kicad_sch Memory File: Memory.kicad_sch USB

4 Y1 48Mhz Quartz Crystal TP9 GND GND

Load: 10pF ESR: 60 ohms Max drive: 100 uW

External LSE Clk (Optional)

Load: 7pF ESR: 50k ohms Max drive: 1 uW

sync CPU Sleep State to

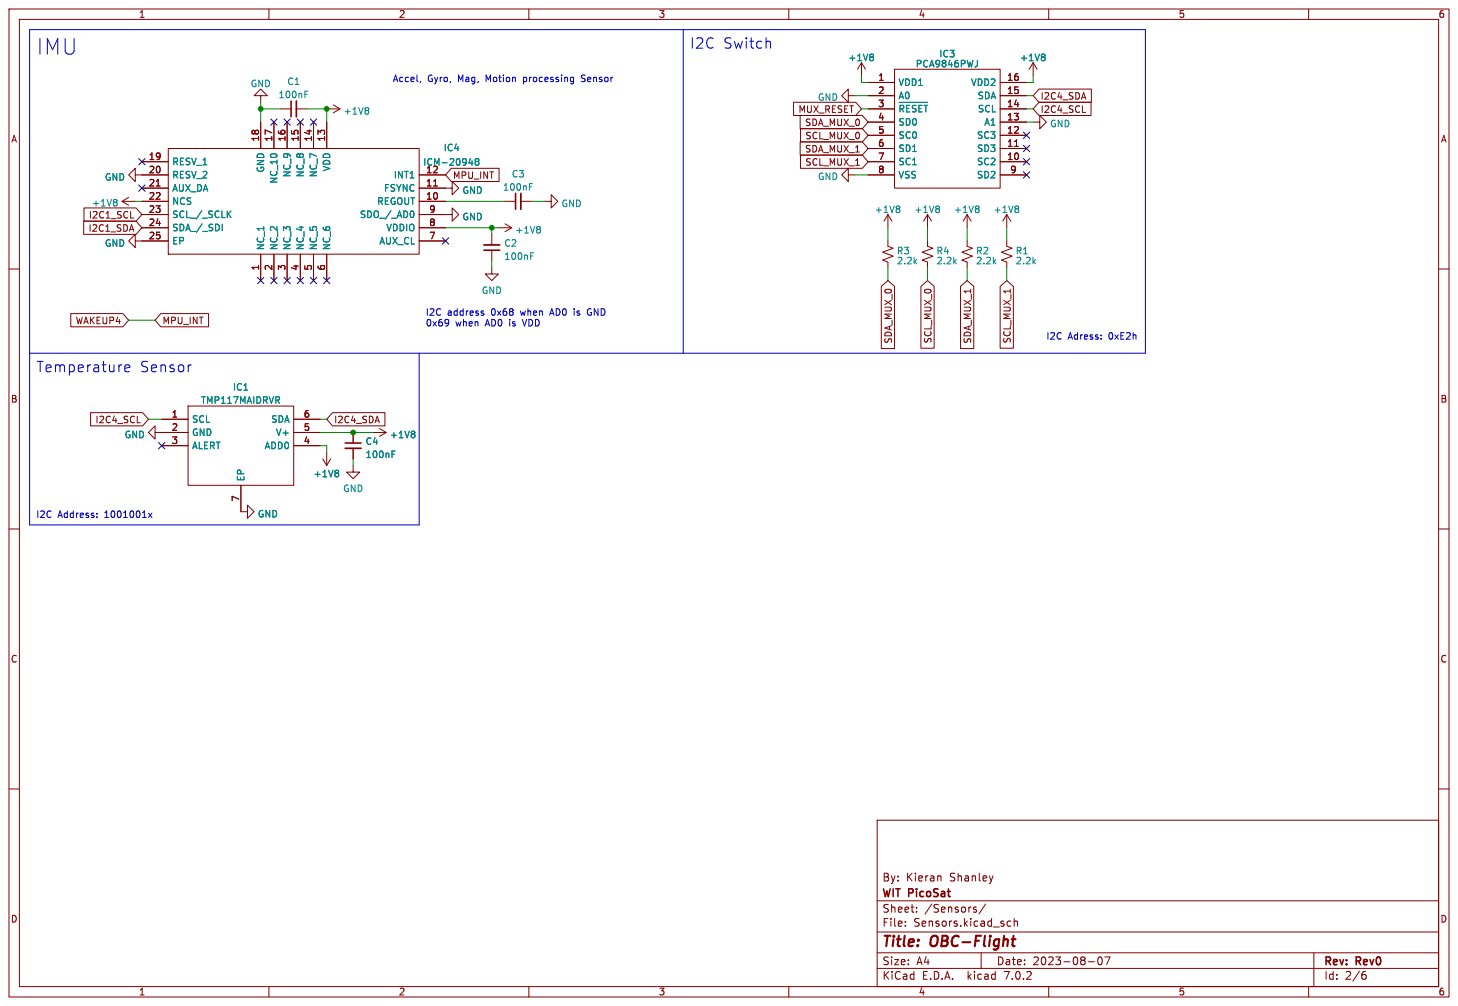
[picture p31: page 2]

I2C address 0x68 when AD0 is GND
0x69 when AD0 is VDD

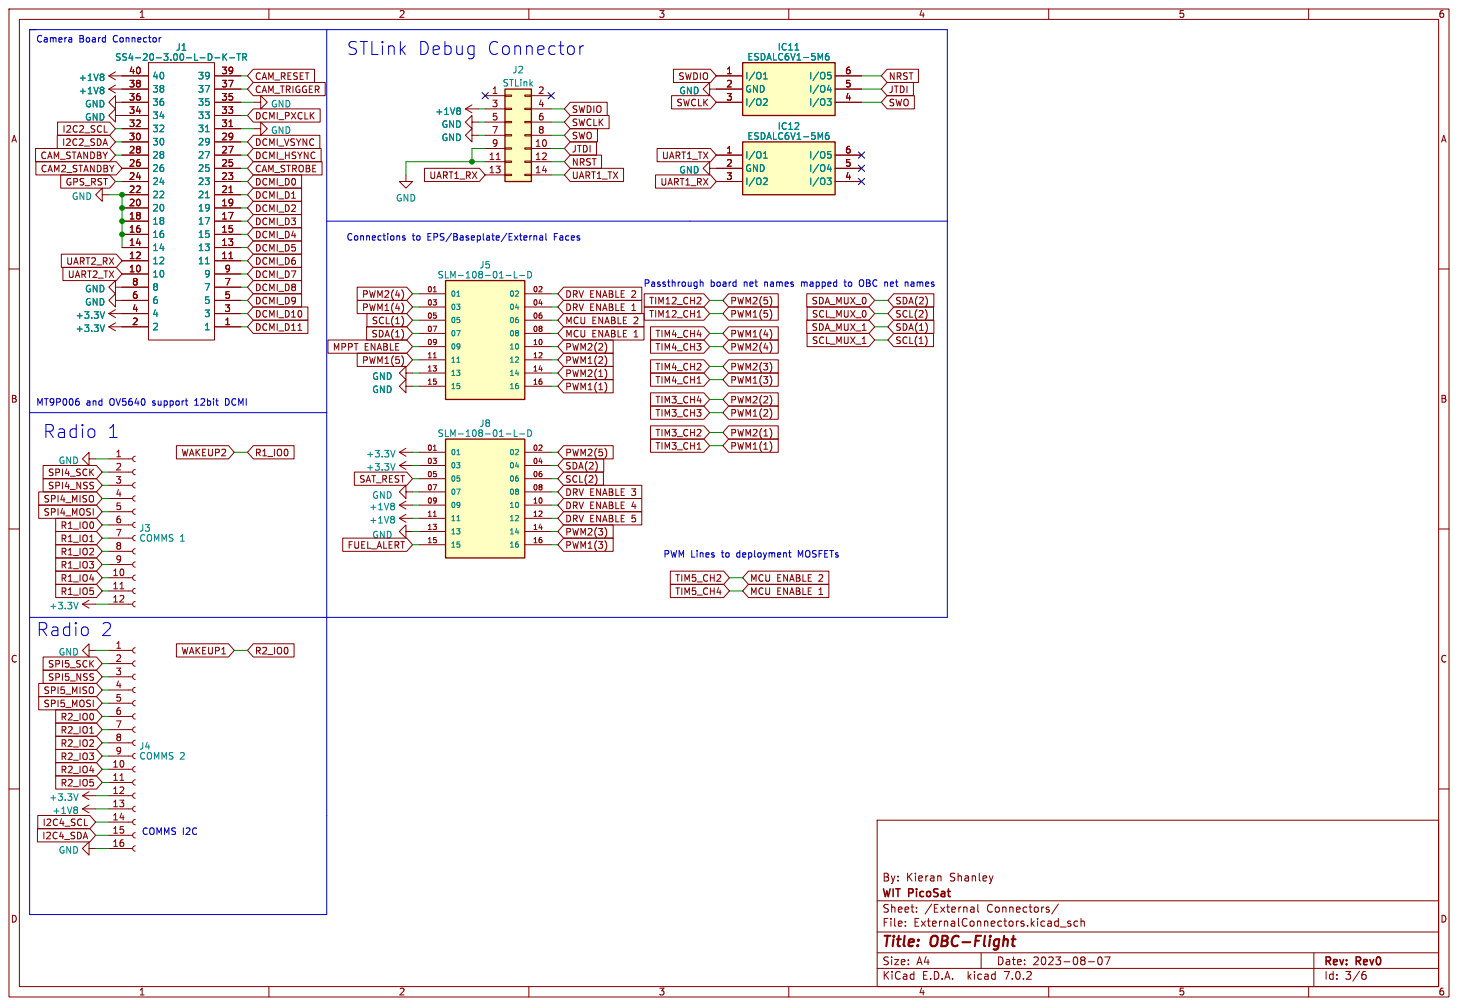
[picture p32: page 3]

Camera Board Connector Radio 2
CAM_RESET SPI5_MISO
GND

PWM2(2) MCU ENABLE 2 DRV ENABLE 2 DRV ENABLE 3 DRV ENABLE 4 PWM2(3)
PWM2(5) MCU ENABLE 1 DRV ENABLE 1 PWM1(2)

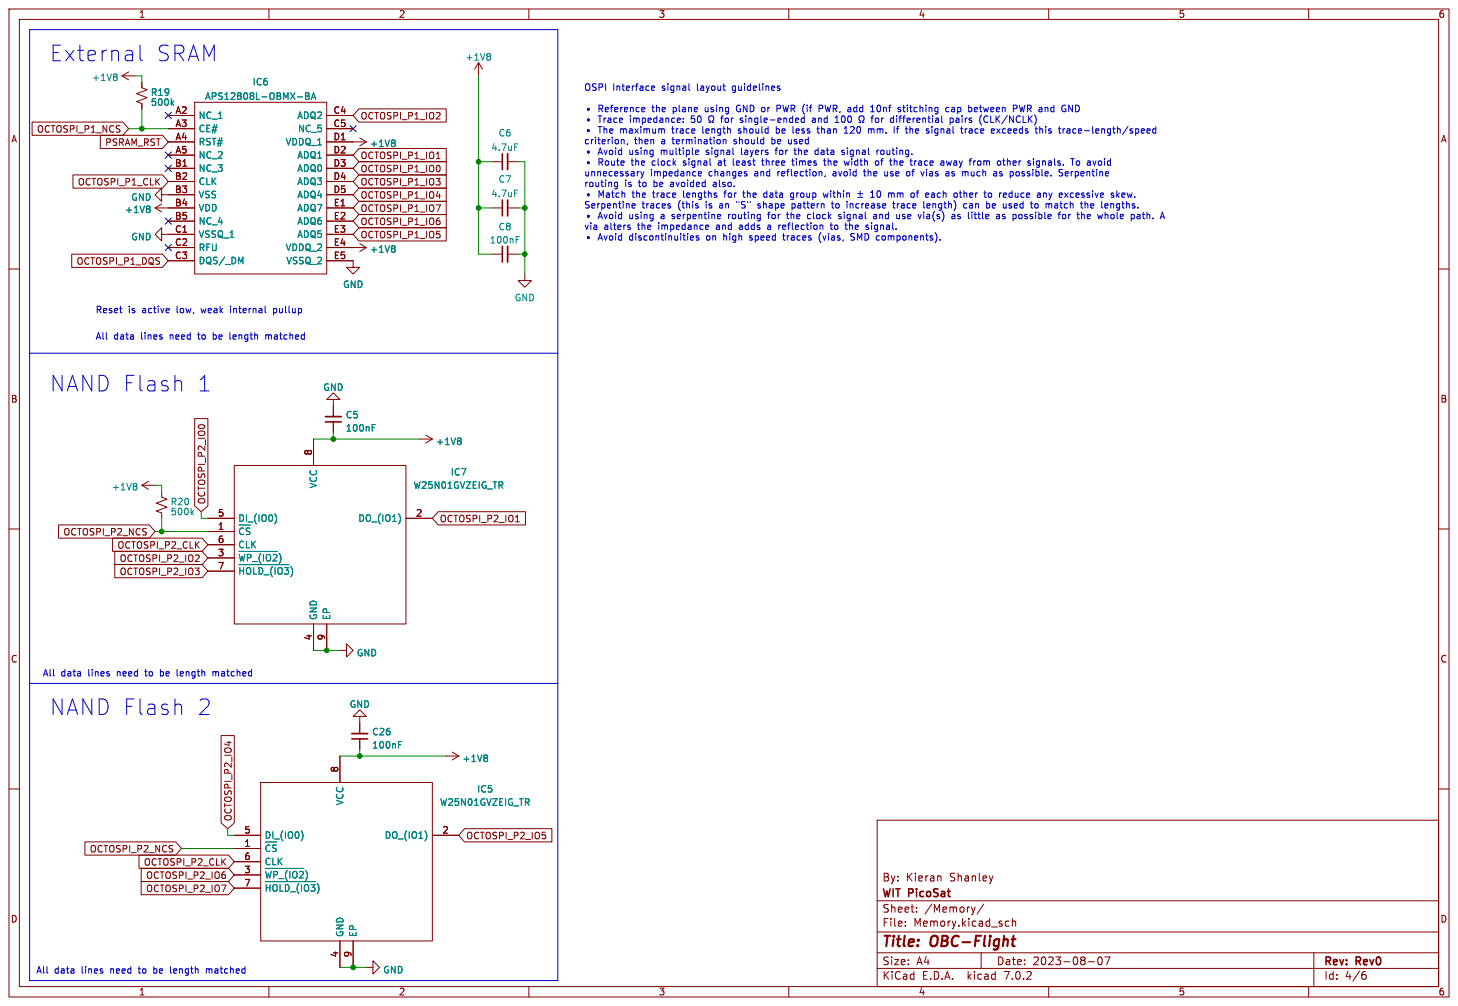
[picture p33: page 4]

All data lines need to be length matched External SRAM
+1V8 GND
500k +1V8 GND
OCTOSPI_P1_DQS NAND Flash 2

þÿ "The maximum trace length should be less than 120 mm. If the signal trace exceeds this trace-length/speed
þÿ "Route the clock signal at least three times the width of the trace away from other signals. To avoid
4.7uFGND

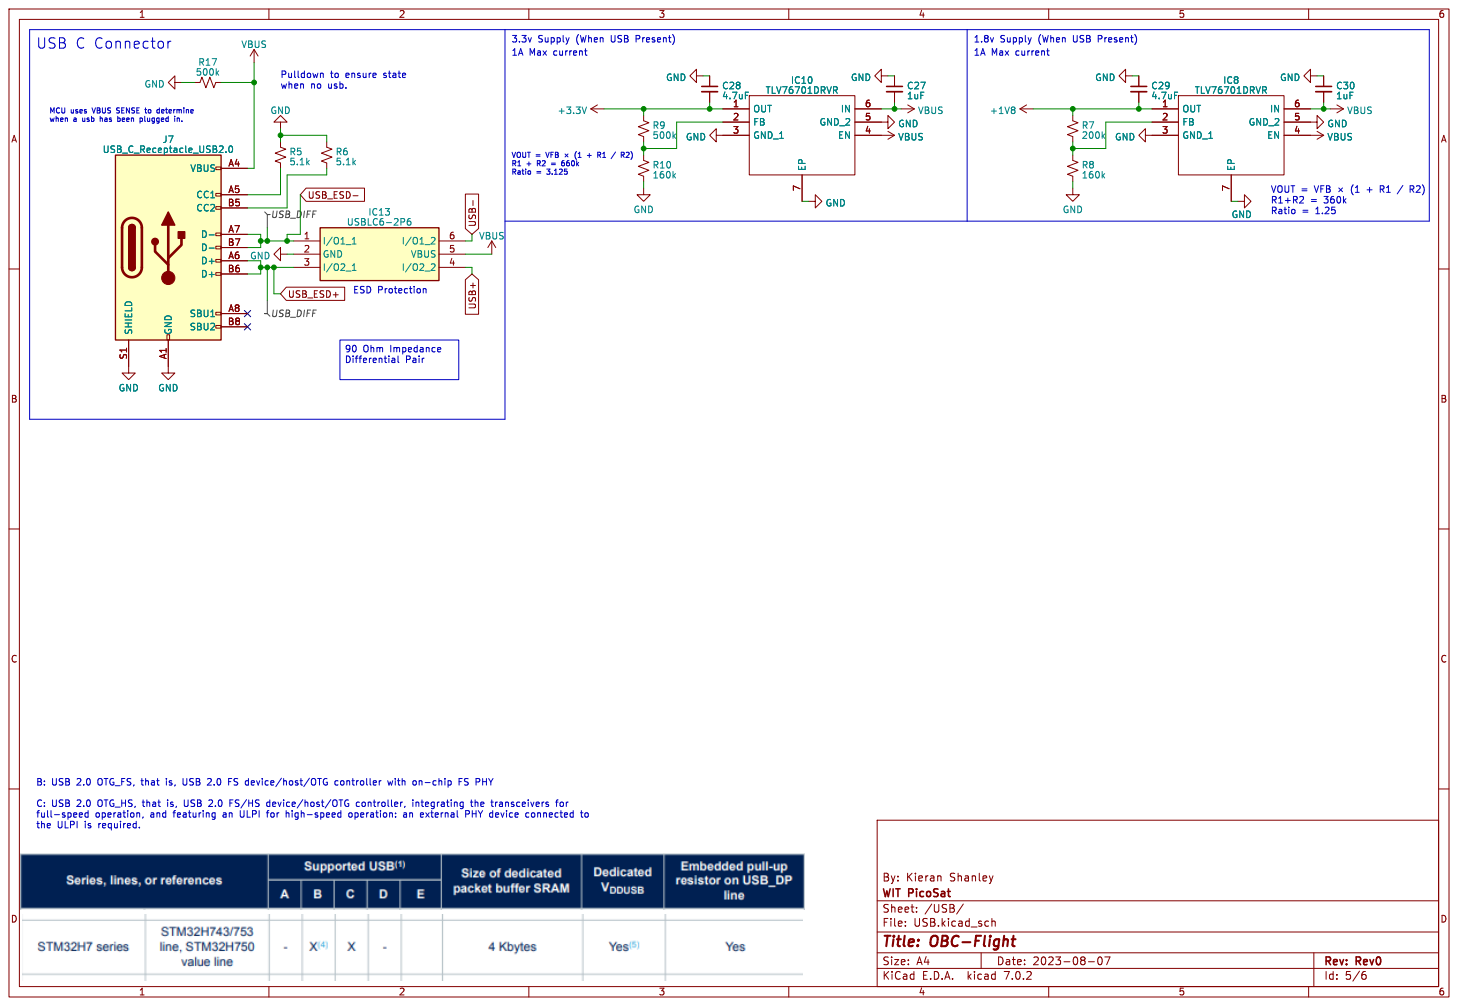
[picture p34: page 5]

the ULPI is required.

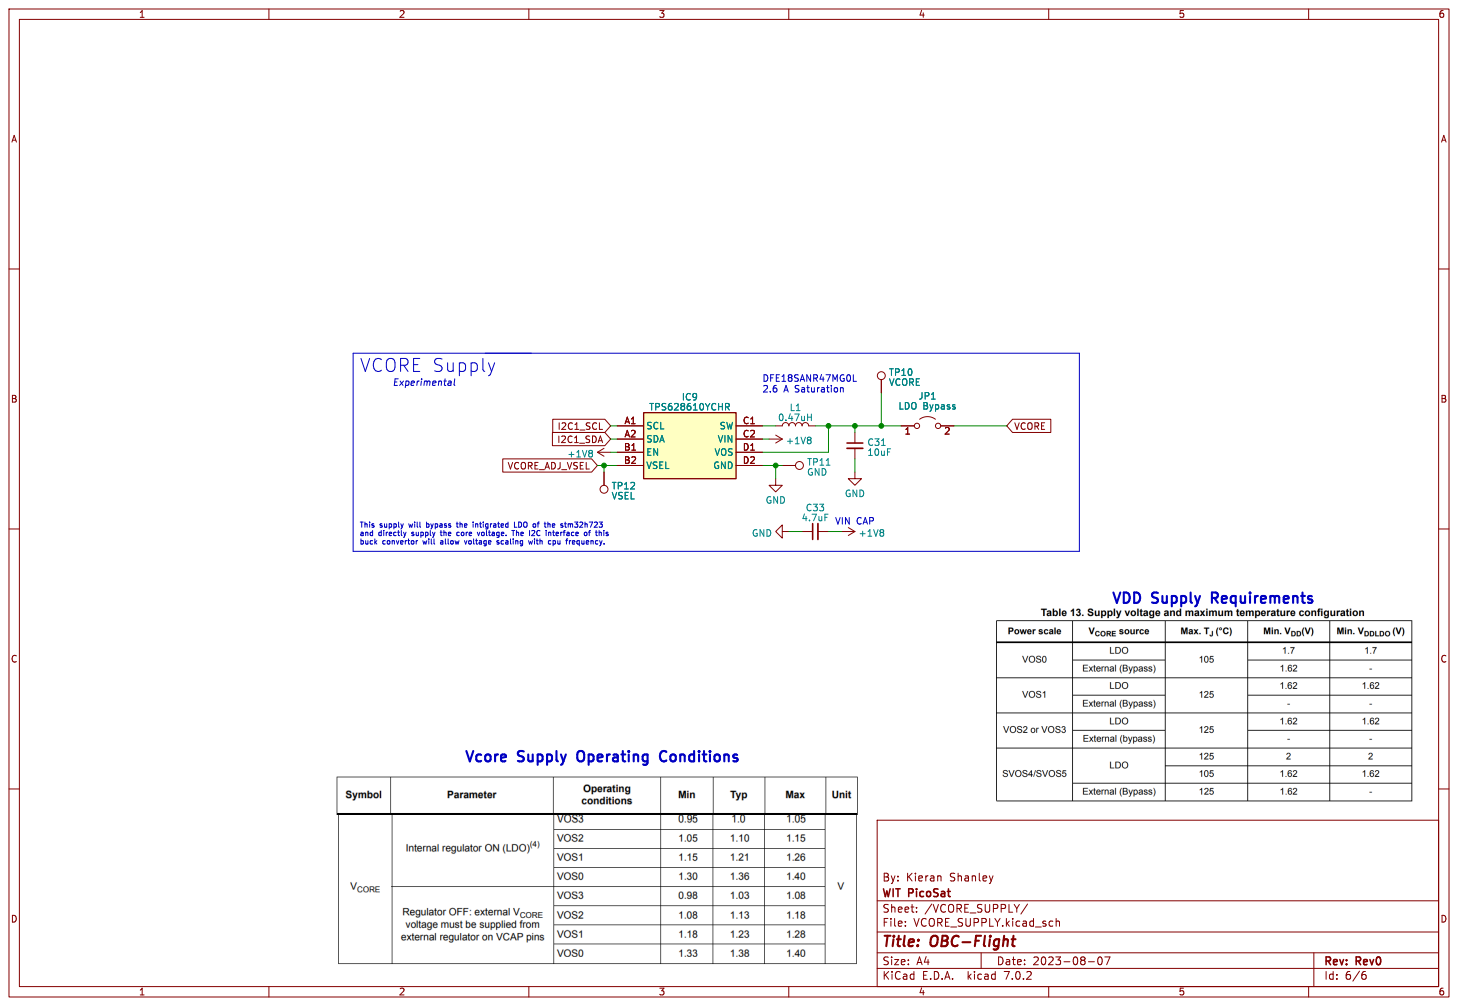
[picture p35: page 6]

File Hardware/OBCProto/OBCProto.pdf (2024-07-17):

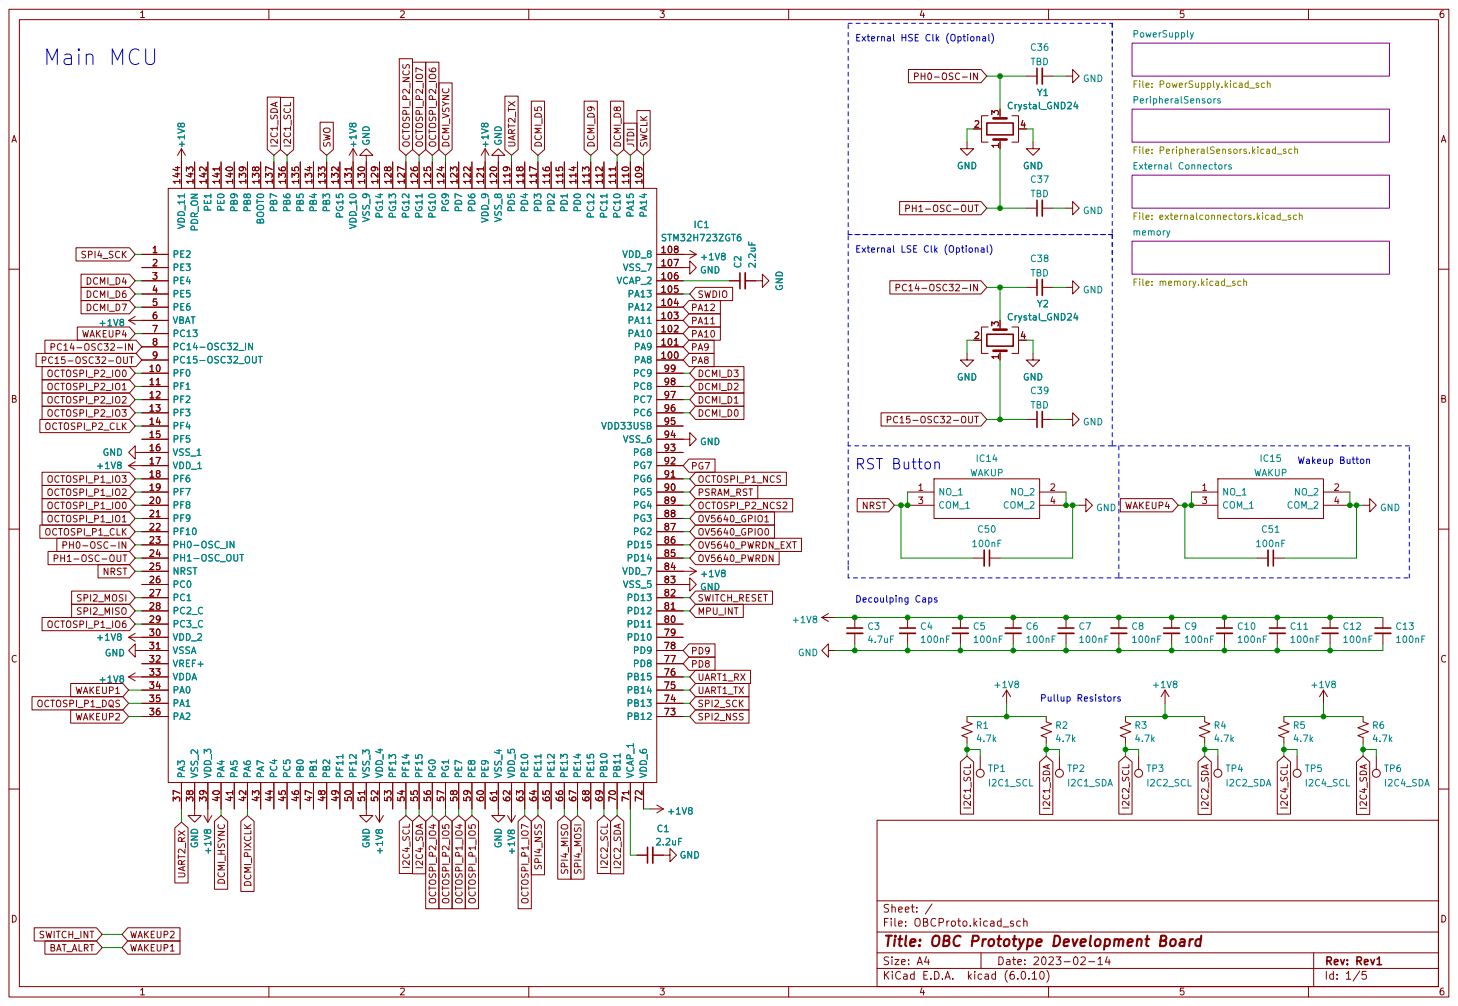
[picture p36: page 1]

External HSE Clk (Optional)

File: PeripheralSensors.kicad_sch memory File: memory.kicad_sch External Connectors File: externalconnectors.kicad_sch PowerSupply
4GND GND

External LSE Clk (Optional) | | C38 TBD

Wakeup Button

File: OBCProto.kicad_sch Sheet: /
Id: 1/5 Title: OBC Prototype Development Board

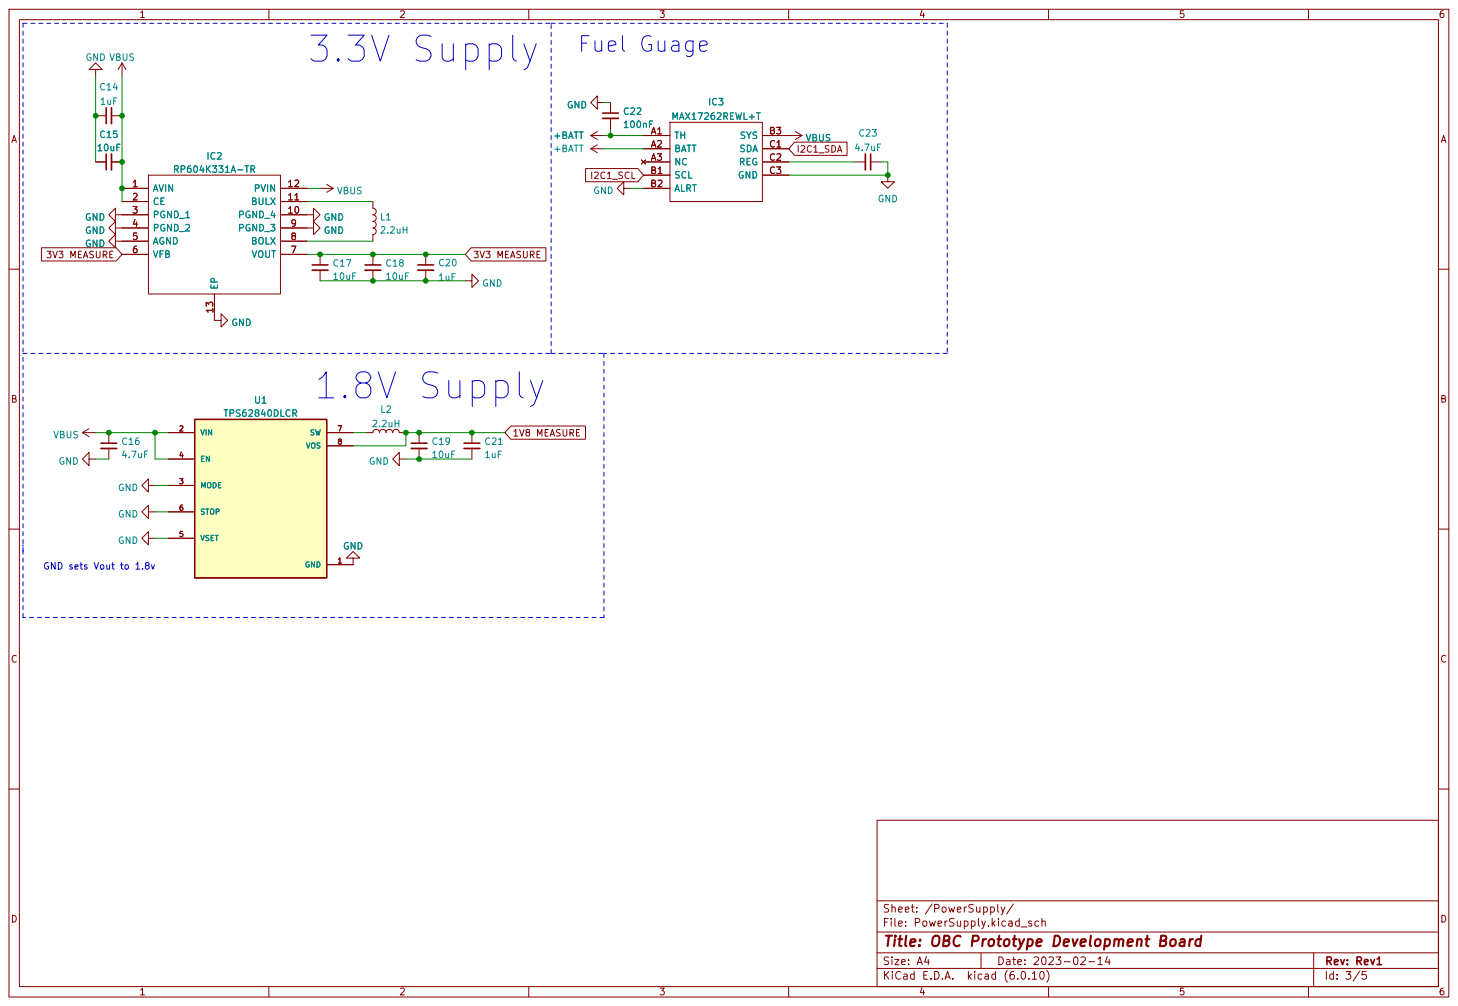
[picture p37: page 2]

Sheet: /PowerSupply/
File: PowerSupply.kicad_sch
Id: 3/5 Title: OBC Prototype Development Board

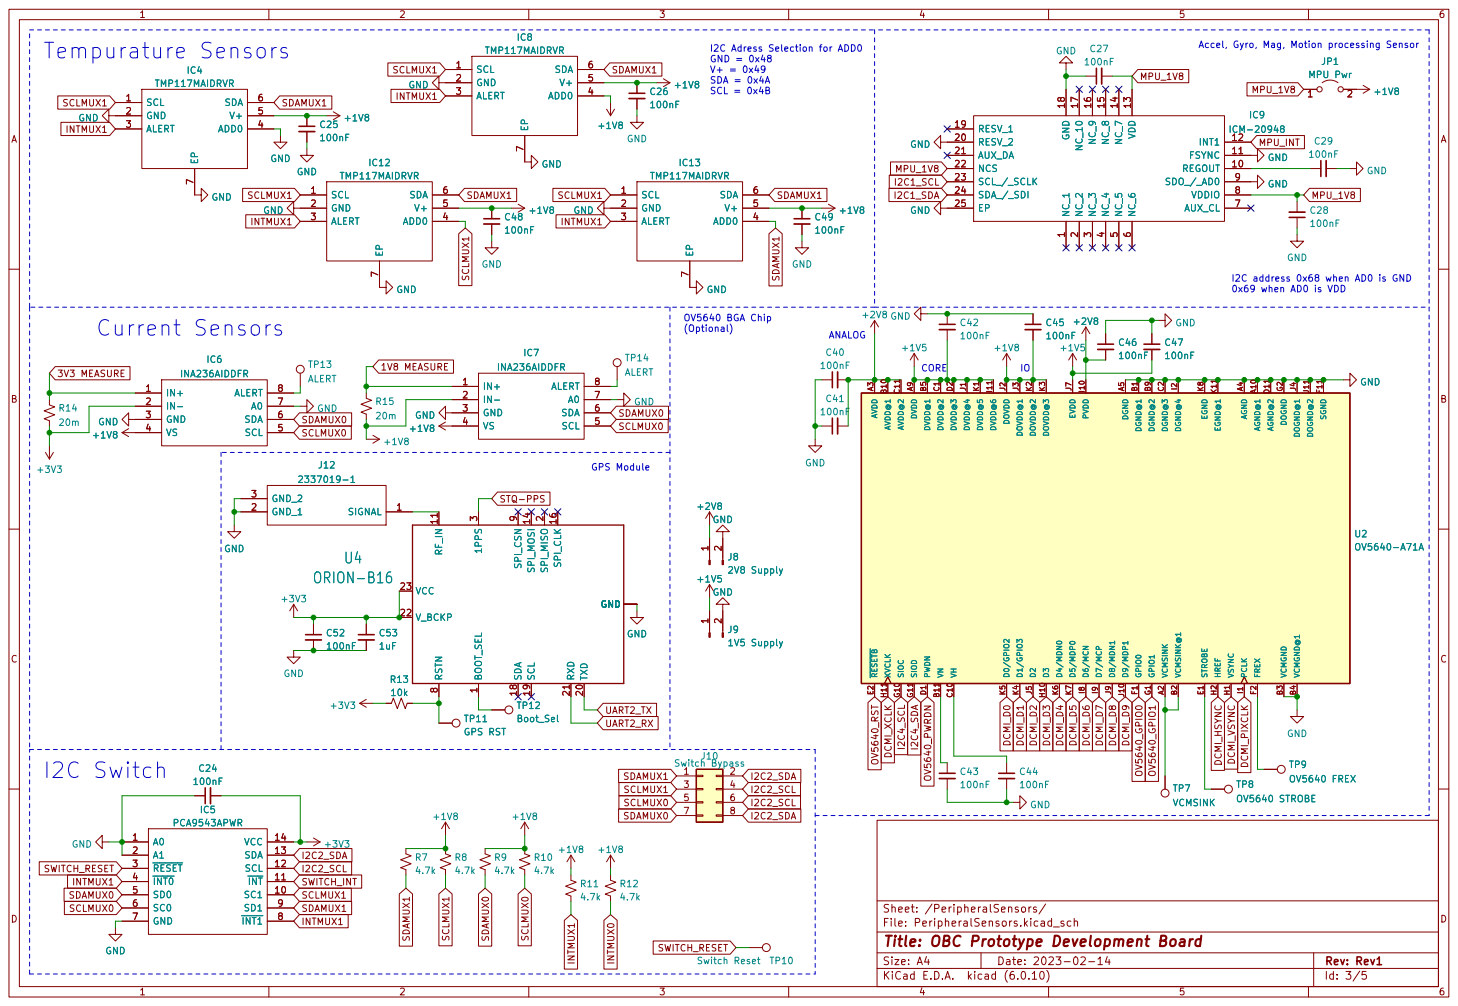
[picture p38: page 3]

I2C Adress Selection for ADD0 GND = 0x48 V+ = 0x49 SDA = 0x4A

I2C address 0x68 when AD0 is GND
0x69 when AD0 is VDD
TP9 OV5640 FREX GND

2 TXD 20 RXD 21 V_BCKP 22 VCC 23 GND 1PPS

Sheet: /PeripheralSensors/
File: PeripheralSensors.kicad_sch
Id: 3/5 Title: OBC Prototype Development Board

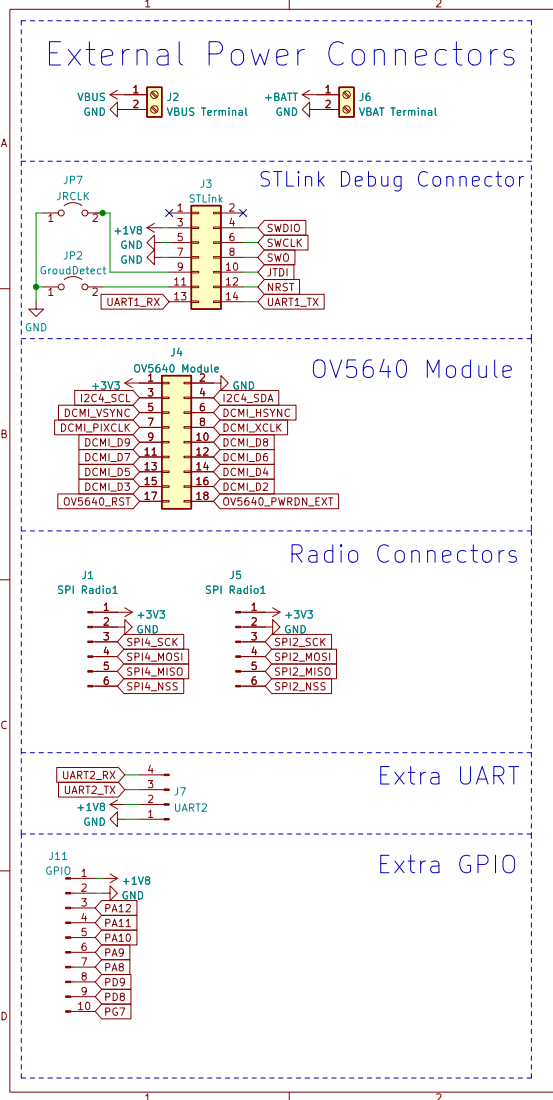
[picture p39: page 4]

File: externalconnectors.kicad_sch Sheet: /External Connectors/
Id: 4/5 Title: OBC Prototype Development Board

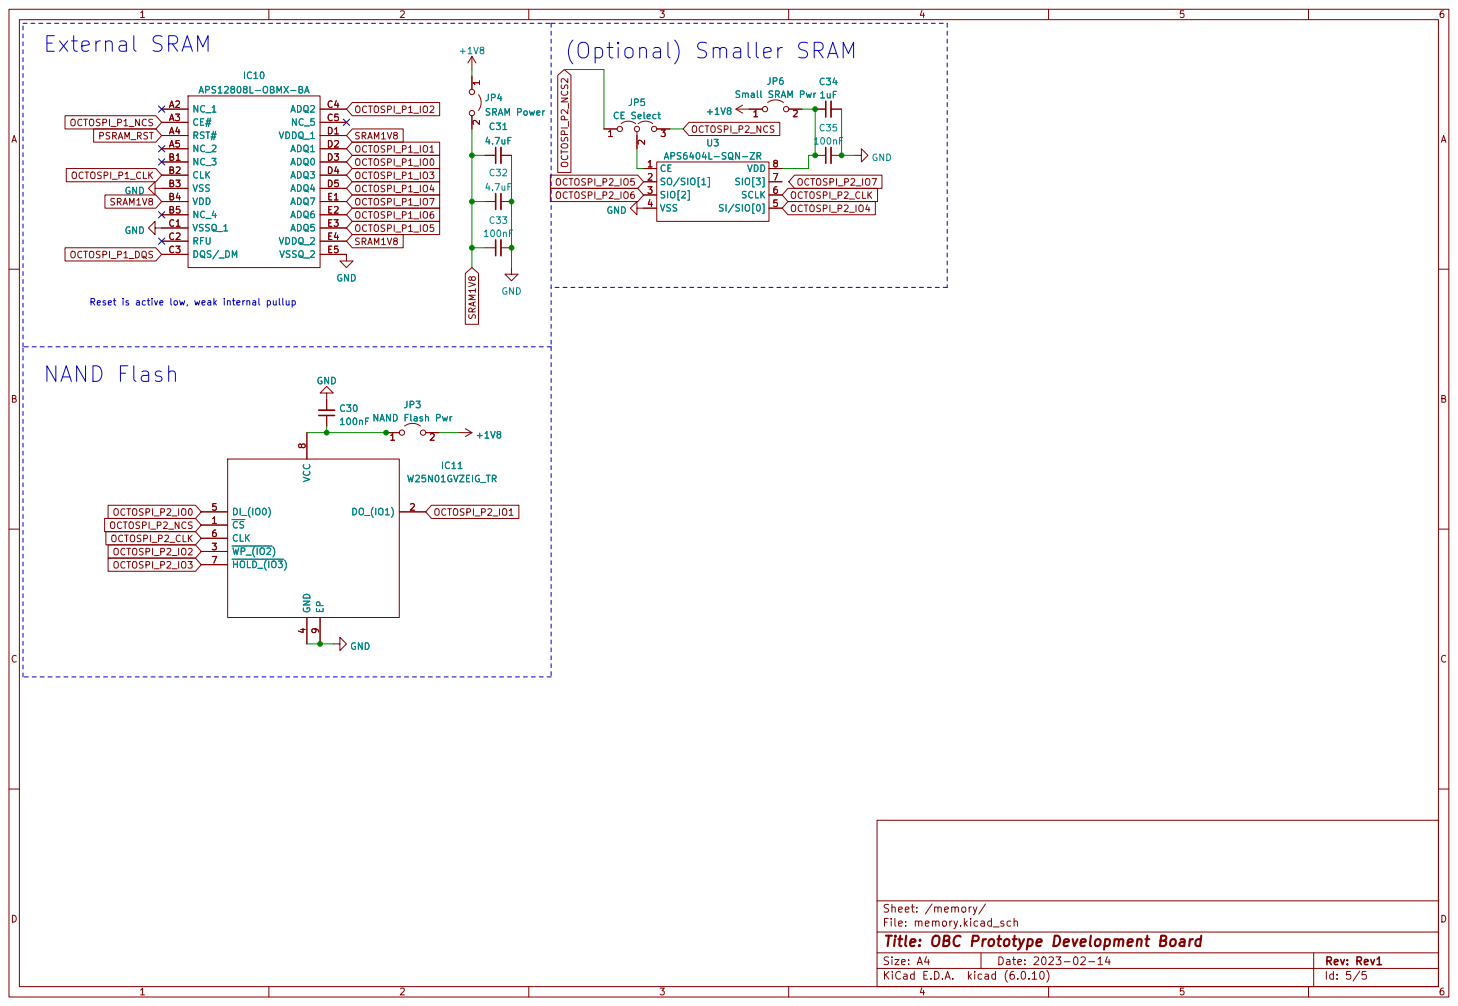
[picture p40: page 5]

JP6 Small SRAM Pwr GND
1uF GND GND GND

JP3 NAND Flash Pwr GND

Reset is active low, weak internal pullup

Sheet: /memory/
File: memory.kicad_sch
Id: 5/5 Title: OBC Prototype Development Board

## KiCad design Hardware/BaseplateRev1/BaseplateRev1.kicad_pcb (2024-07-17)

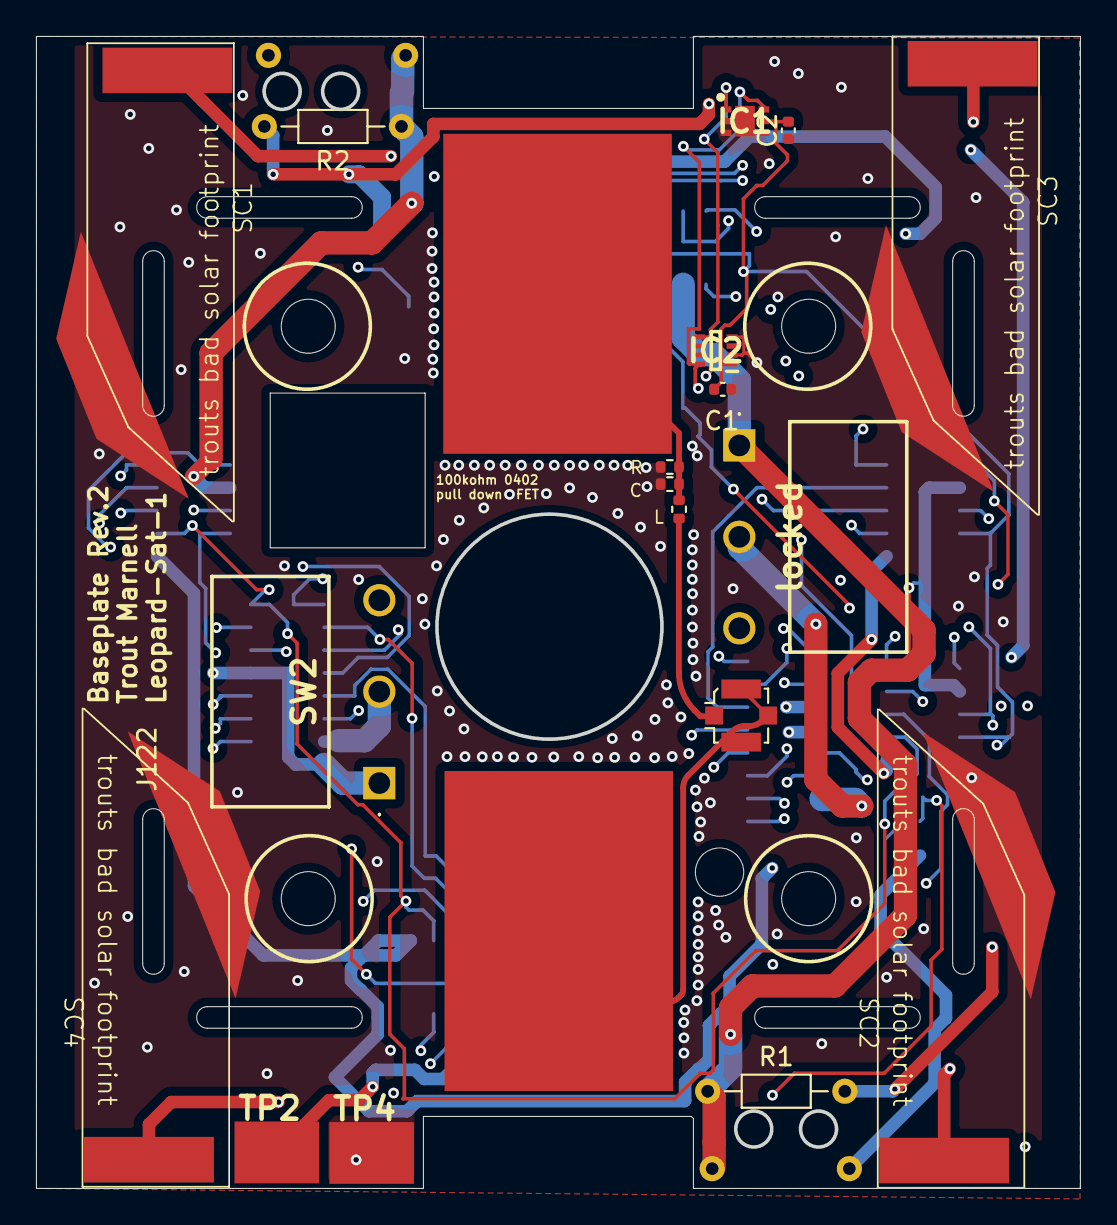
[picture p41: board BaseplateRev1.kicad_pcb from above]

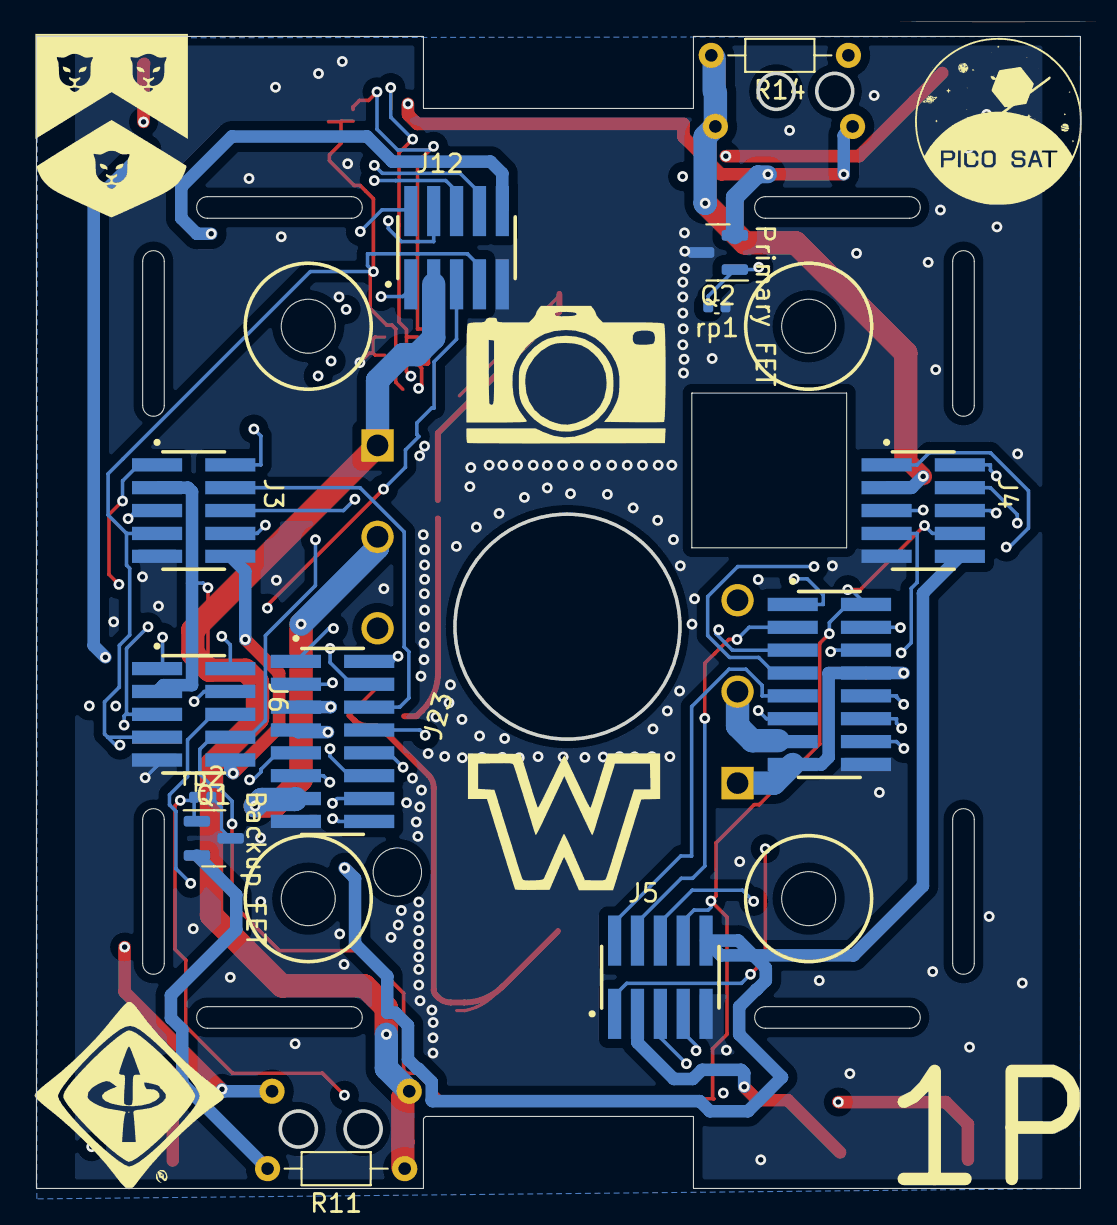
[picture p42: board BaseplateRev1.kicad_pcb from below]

Board: 4 copper layers, 58.0 x 64.0 mm, 33 parts (13 on the bottom side), 33 nets.

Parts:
C1, C2: 0.1uF; C_0402_1005Metric
IC1: TMP117MAIDRVR; SON65P200X200X80-7N
IC2: OPT4048DTSR; SOTFL50P190X60-8N
J3, J4, J5, J6, J12: FTSH-105-XX-X-DV; SAMTEC_FTSH-105-XX-X-DV
J8: Conn_Coaxial; U.FL_Molex_MCRF_73412-0110_Vertical
J23, J122: FLE-108-01-XX-DV; SAMTEC_FW-08-03-G-D-335-065
Q1, Q2: 2N7002; SOT-23
R1, R2, R11, R14: R_Small_US; R_Axial_DIN0204_L3.6mm_D1.6mm_P7.62mm_Horizontal
REF5554: R_0402_1005Metric
REFW: R_0402_1005Metric
REFinduc: R_0402_1005Metric
SC1, SC2, SC3, SC4: Solar_Cell; solar
SW2: SW_SPDT; D2FA1
TP2, TP4: TestPoint; 5016
U1, U2: antenna
locked: SW_SPDT; D2FA1
rp1, rp2: 100k; C_0402_1005Metric

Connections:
1.8V: C1.2, C2.2, IC1.5 (V+), IC2.1 (VDD), J3.07, J4.07, J5.07, J6.07, J12.07, J23.11, J122.14
Battery +: J3.03, J4.03, J5.03, J6.03, J12.03, J122.08, J122.15, R1.1, R2.1, R11.1, R14.2, SW2.1 (A), TP2.1, locked.1 (A)
Coaxout: J8.1 (In), REFinduc.1
DRV ENABLE 1: J4.04, J122.01
DRV ENABLE 2: J5.04, J122.03
DRV ENABLE 3: J6.04, J23.10
DRV ENABLE 4: J12.04, J23.08
DRV ENABLE 5: J3.04, J23.06
GND: C1.1, C2.1, IC1.2 (GND), IC1.3 (ALERT), IC1.4 (ADD0), IC1.7 (EP), IC2.2 (ADDR), IC2.4 (GND), J3.09, J4.09, J5.09, J6.09, J12.09, J23.15, J122.16, Q1.3 (D), Q2.3 (D), REF5554.1, REFW.1, SC1.2 (-), SC2.2 (-), SC3.2 (-), SC4.2 (-), TP4.1, rp1.1, rp2.2
MCU ENABLE 1: J122.07, Q2.1 (G), rp1.2
MCU ENABLE 2: J122.05, Q1.1 (G), rp2.1
MPPT ENABLE: J3.06, J4.06, J5.06, J6.06, J12.06, J122.06
unnamed: Q1.2 (S), R11.2, R14.1
unnamed: Q2.2 (S), R1.2, R2.2
PWM1(1): J4.01, J122.10
PWM1(2): J5.01, J122.11
PWM1(3): J6.01, J23.02
PWM1(4): J12.01, J23.03
PWM1(5): J3.01, J23.09
PWM2(1): J4.02, J122.12
PWM2(2): J5.02, J122.09
PWM2(3): J6.02, J23.04
PWM2(4): J12.02, J23.01
PWM2(5): J3.02, J23.16
RF ANTENNA: REF5554.2, REFW.2, REFinduc.2, U2.1 (RF_IN)
SCL(1): J4.08, J5.08, J6.08, J12.08, J122.02
SCL(2): IC1.1 (SCL), IC2.5 (SCL), J3.08, J23.12
SDA(1): J4.05, J5.05, J6.05, J12.05, J122.04
SDA(2): IC1.6 (SDA), IC2.8 (SDA), J3.05, J23.14
VBAT+: J23.13, J122.13, SW2.2 (B), locked.2 (B)
VMPPT: J3.10, J4.10, J5.10, J6.10, J12.10, J23.07
Vsolar: J23.05, SC1.1 (+), SC2.1 (+), SC3.1 (+), SC4.1 (+)
rfgnd: J8.2 (Ext), U1.1 (RF_IN)

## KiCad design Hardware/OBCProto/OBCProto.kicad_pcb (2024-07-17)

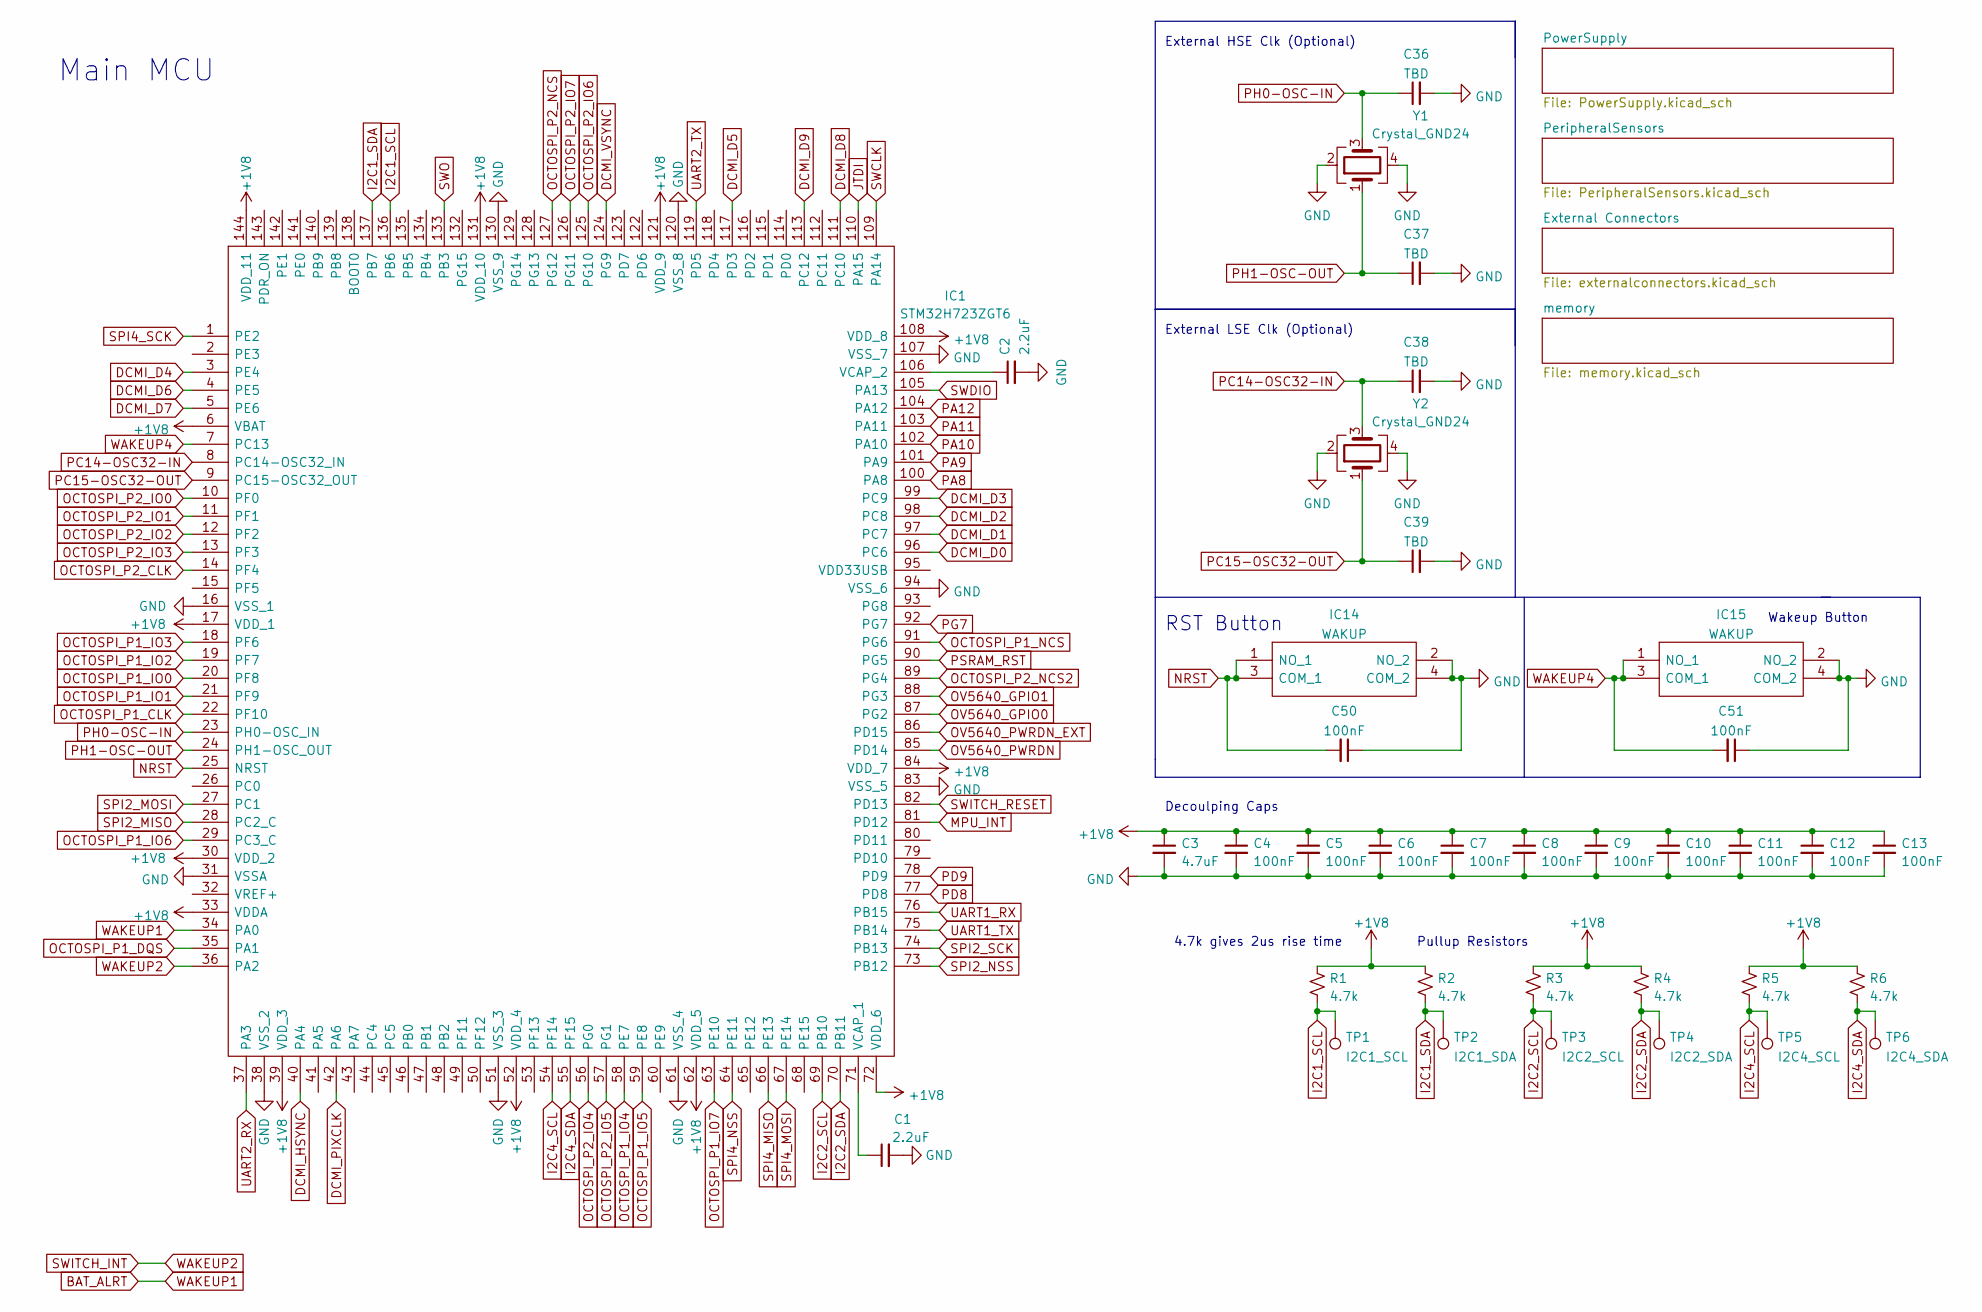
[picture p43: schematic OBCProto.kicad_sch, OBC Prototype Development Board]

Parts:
C1, C2: 2.2uF; C_0402_1005Metric
C3: 4.7uF; C_0402_1005Metric
C4, C5, C6, C7, C8, C9, C10, C11, C12, C13, C50, C51: 100nF; C_0402_1005Metric
C36, C37, C38, C39: TBD; C_0402_1005Metric
IC1: STM32H723ZGT6; QFP50P2200X2200X160-144N; Mouser Part Number 511-STM32H723ZGT6
IC14, IC15: WAKUP; TS046675BK160SMT; Mouser Part Number 179-TS046675BK160SMT
R1, R2, R3, R4, R5, R6: 4.7k; R_0402_1005Metric
TP1: I2C1_SCL; TestPoint_Pad_2.0x2.0mm
TP2: I2C1_SDA; TestPoint_Pad_2.0x2.0mm
TP3: I2C2_SCL; TestPoint_Pad_2.0x2.0mm
TP4: I2C2_SDA; TestPoint_Pad_2.0x2.0mm
TP5: I2C4_SCL; TestPoint_Pad_2.0x2.0mm
TP6: I2C4_SDA; TestPoint_Pad_2.0x2.0mm
Y1, Y2: Crystal_GND24; Crystal_SMD_2520-4Pin_2.5x2.0mm

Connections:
+1V8: C3.1, C4.1, C5.1, C6.1, C7.1, C8.1, C9.1, C10.1, C11.1, C12.1, C13.1, IC1.6 (VBAT), IC1.17 (VDD_1), IC1.30 (VDD_2), IC1.33 (VDDA), IC1.39 (VDD_3), IC1.52 (VDD_4), IC1.62 (VDD_5), IC1.72 (VDD_6), IC1.84 (VDD_7), IC1.108 (VDD_8), IC1.121 (VDD_9), IC1.131 (VDD_10), IC1.144 (VDD_11), R1.1, R2.1, R3.1, R4.1, R5.1, R6.1; also elsewhere on the board
BAT_ALRT: IC1.34 (PA0)
DCMI_D0: IC1.96 (PC6); also elsewhere on the board
DCMI_D1: IC1.97 (PC7); also elsewhere on the board
DCMI_D2: IC1.98 (PC8); also elsewhere on the board
DCMI_D3: IC1.99 (PC9); also elsewhere on the board
DCMI_D4: IC1.3 (PE4); also elsewhere on the board
DCMI_D5: IC1.117 (PD3); also elsewhere on the board
DCMI_D6: IC1.4 (PE5); also elsewhere on the board
DCMI_D7: IC1.5 (PE6); also elsewhere on the board
DCMI_D8: IC1.111 (PC10); also elsewhere on the board
DCMI_D9: IC1.113 (PC12); also elsewhere on the board
DCMI_HSYNC: IC1.40 (PA4); also elsewhere on the board
DCMI_PIXCLK: IC1.42 (PA6); also elsewhere on the board
DCMI_VSYNC: IC1.124 (PG9); also elsewhere on the board
GND: C1.2, C2.2, C3.2, C4.2, C5.2, C6.2, C7.2, C8.2, C9.2, C10.2, C11.2, C12.2, C13.2, C36.2, C37.2, C38.2, C39.2, C50.1, C51.1, IC1.16 (VSS_1), IC1.31 (VSSA), IC1.38 (VSS_2), IC1.51 (VSS_3), IC1.61 (VSS_4), IC1.83 (VSS_5), IC1.94 (VSS_6), IC1.107 (VSS_7), IC1.120 (VSS_8), IC1.130 (VSS_9), IC14.2 (NO_2), IC14.4 (COM_2), IC15.2 (NO_2), IC15.4 (COM_2), Y1.2, Y1.4, Y2.2, Y2.4; also elsewhere on the board
I2C1_SCL: IC1.136 (PB6), R1.2, TP1.1; also elsewhere on the board
I2C1_SDA: IC1.137 (PB7), R2.2, TP2.1; also elsewhere on the board
I2C2_SCL: IC1.69 (PB10), R3.2, TP3.1; also elsewhere on the board
I2C2_SDA: IC1.70 (PB11), R4.2, TP4.1; also elsewhere on the board
I2C4_SCL: IC1.54 (PF14), R5.2, TP5.1; also elsewhere on the board
I2C4_SDA: IC1.55 (PF15), R6.2, TP6.1; also elsewhere on the board
JTDI: IC1.110 (PA15); also elsewhere on the board
MPU_INT: IC1.81 (PD12); also elsewhere on the board
NRST: C50.2, IC1.25 (NRST), IC14.1 (NO_1), IC14.3 (COM_1); also elsewhere on the board
unnamed: C1.1, IC1.71 (VCAP_1)
unnamed: C2.1, IC1.106 (VCAP_2)
OCTOSPI_P1_CLK: IC1.22 (PF10); also elsewhere on the board
OCTOSPI_P1_DQS: IC1.35 (PA1); also elsewhere on the board
OCTOSPI_P1_IO0: IC1.20 (PF8); also elsewhere on the board
OCTOSPI_P1_IO1: IC1.21 (PF9); also elsewhere on the board
OCTOSPI_P1_IO2: IC1.19 (PF7); also elsewhere on the board
OCTOSPI_P1_IO3: IC1.18 (PF6); also elsewhere on the board
OCTOSPI_P1_IO4: IC1.58 (PE7); also elsewhere on the board
OCTOSPI_P1_IO5: IC1.59 (PE8); also elsewhere on the board
OCTOSPI_P1_IO6: IC1.29 (PC3_C); also elsewhere on the board
OCTOSPI_P1_IO7: IC1.63 (PE10); also elsewhere on the board
OCTOSPI_P1_NCS: IC1.91 (PG6); also elsewhere on the board
OCTOSPI_P2_CLK: IC1.14 (PF4); also elsewhere on the board
OCTOSPI_P2_IO0: IC1.10 (PF0); also elsewhere on the board
OCTOSPI_P2_IO1: IC1.11 (PF1); also elsewhere on the board
OCTOSPI_P2_IO2: IC1.12 (PF2); also elsewhere on the board
OCTOSPI_P2_IO3: IC1.13 (PF3); also elsewhere on the board
OCTOSPI_P2_IO4: IC1.56 (PG0); also elsewhere on the board
OCTOSPI_P2_IO5: IC1.57 (PG1); also elsewhere on the board
OCTOSPI_P2_IO6: IC1.125 (PG10); also elsewhere on the board
OCTOSPI_P2_IO7: IC1.126 (PG11)
OCTOSPI_P2_NCS: IC1.127 (PG12); also elsewhere on the board
OCTOSPI_P2_NCS2: IC1.89 (PG4); also elsewhere on the board
OV5640_GPIO0: IC1.87 (PG2); also elsewhere on the board
OV5640_GPIO1: IC1.88 (PG3); also elsewhere on the board
OV5640_PWRDN: IC1.85 (PD14); also elsewhere on the board
OV5640_PWRDN_EXT: IC1.86 (PD15); also elsewhere on the board
PA8: IC1.100 (PA8); also elsewhere on the board
PA9: IC1.101 (PA9); also elsewhere on the board
PA10: IC1.102 (PA10); also elsewhere on the board
PA11: IC1.103 (PA11); also elsewhere on the board
PA12: IC1.104 (PA12); also elsewhere on the board
PC14-OSC32-IN: C38.1, IC1.8 (PC14-OSC32_IN), Y2.3
PC15-OSC32-OUT: C39.1, IC1.9 (PC15-OSC32_OUT), Y2.1
PD8: IC1.77 (PD8); also elsewhere on the board
PD9: IC1.78 (PD9); also elsewhere on the board
PG7: IC1.92 (PG7); also elsewhere on the board
PH0-OSC-IN: C36.1, IC1.23 (PH0-OSC_IN), Y1.3
PH1-OSC-OUT: C37.1, IC1.24 (PH1-OSC_OUT), Y1.1
PSRAM_RST: IC1.90 (PG5); also elsewhere on the board
SPI2_MISO: IC1.28 (PC2_C); also elsewhere on the board
SPI2_MOSI: IC1.27 (PC1); also elsewhere on the board
SPI2_NSS: IC1.73 (PB12); also elsewhere on the board
SPI2_SCK: IC1.74 (PB13); also elsewhere on the board
SPI4_MISO: IC1.66 (PE13); also elsewhere on the board
SPI4_MOSI: IC1.67 (PE14); also elsewhere on the board
SPI4_NSS: IC1.64 (PE11); also elsewhere on the board
SPI4_SCK: IC1.1 (PE2); also elsewhere on the board
SWCLK: IC1.109 (PA14); also elsewhere on the board
SWDIO: IC1.105 (PA13); also elsewhere on the board
SWITCH_INT: IC1.36 (PA2); also elsewhere on the board
SWITCH_RESET: IC1.82 (PD13); also elsewhere on the board
SWO: IC1.133 (PB3); also elsewhere on the board
UART1_RX: IC1.76 (PB15); also elsewhere on the board
UART1_TX: IC1.75 (PB14); also elsewhere on the board
UART2_RX: IC1.37 (PA3); also elsewhere on the board
UART2_TX: IC1.119 (PD5); also elsewhere on the board
WAKEUP4: C51.2, IC1.7 (PC13), IC15.1 (NO_1), IC15.3 (COM_1)

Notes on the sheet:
Main MCU
RST Button
Wakeup Button
4.7k gives 2us rise time
Pullup Resistors
External HSE Clk (Optional)
External LSE Clk (Optional)
Decoulping Caps

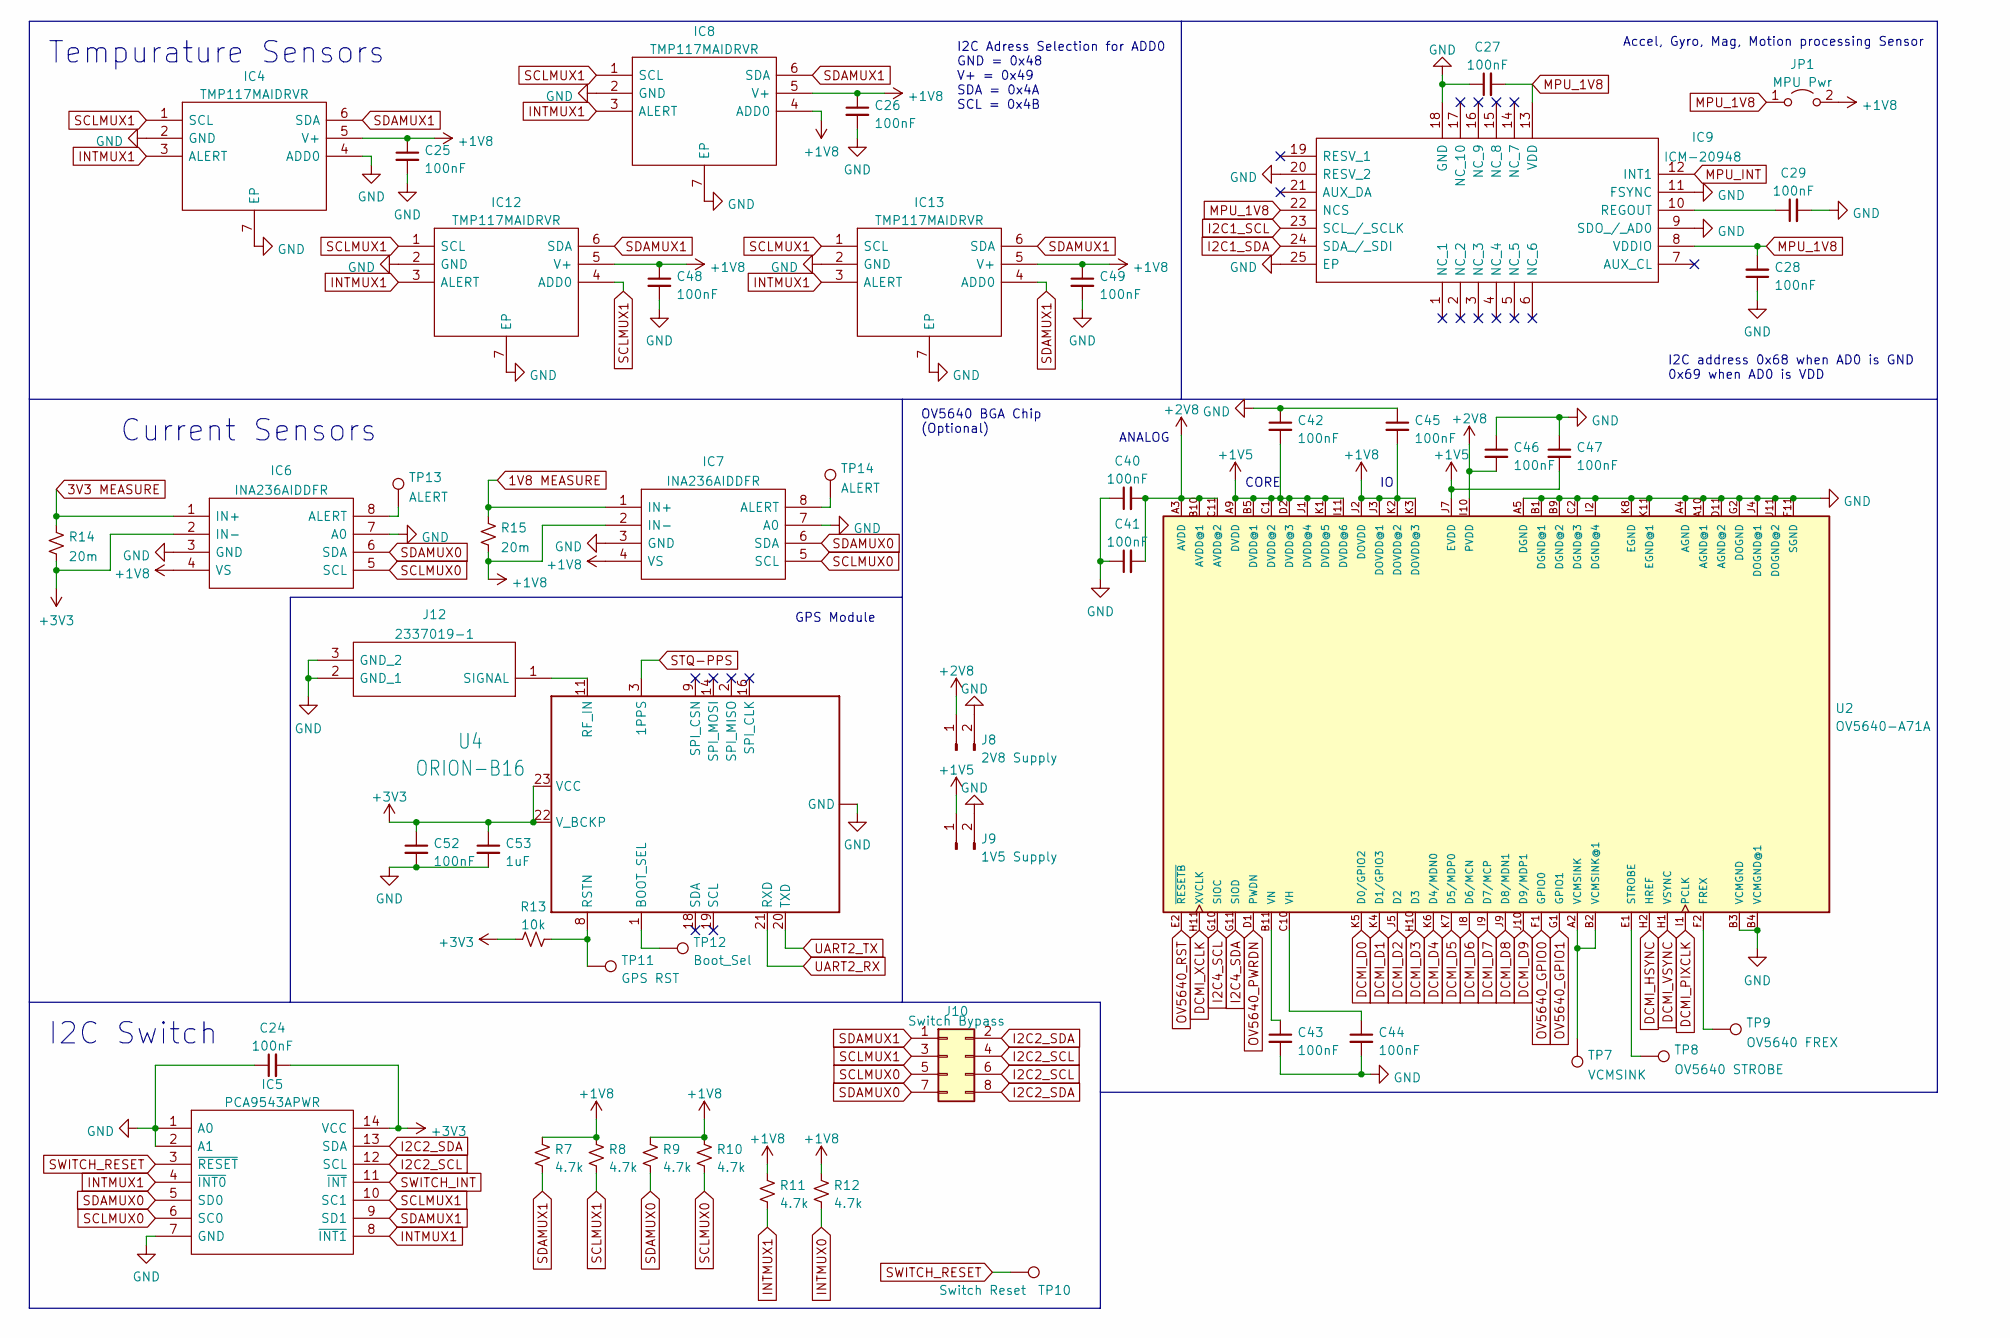
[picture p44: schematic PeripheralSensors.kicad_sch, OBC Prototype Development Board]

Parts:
C24, C25, C26, C27, C28, C29, C40, C41, C42, C43, C44, C45, C46, C47, C48, C49, C52: 100nF; C_0402_1005Metric
C53: 1uF; C_0402_1005Metric
IC4, IC8, IC12, IC13: TMP117MAIDRVR; SON65P200X200X80-7N; Mouser Part Number 595-TMP117MAIDRVR
IC5: PCA9543APWR; SOP65P640X120-14N; Mouser Part Number 595-PCA9543APWR
IC6, IC7: INA236AIDDFR; SOP65P280X110-8N; Manufacturer_Part_Number INA236AIDDFR; Mouser Part Number 595-INA236AIDDFR
IC9: ICM-20948; QFN40P300X300X105-25N-D; Mouser Part Number 410-ICM-20948
J8: 2V8 Supply; PinHeader_1x02_P2.54mm_Vertical
J9: 1V5 Supply; PinHeader_1x02_P2.54mm_Vertical
J10: Switch Bypass; PinHeader_2x04_P2.54mm_Vertical
J12: 2337019-1; 23370191; Mouser Part Number 571-2337019-1
JP1: MPU Pwr; PinHeader_1x02_P2.54mm_Vertical
R7, R8, R9, R10, R11, R12: 4.7k; R_0402_1005Metric
R13: 10k; R_0402_1005Metric
R14, R15: 20m; R_1020_2550Metric
TP7: VCMSINK; TestPoint_Pad_2.0x2.0mm
TP8: OV5640 STROBE; TestPoint_Pad_2.0x2.0mm
TP9: OV5640 FREX; TestPoint_Pad_2.0x2.0mm
TP10: Switch Reset; TestPoint_Pad_2.0x2.0mm
TP11: GPS RST; TestPoint_Pad_1.5x1.5mm
TP12: Boot_Sel; TestPoint_Pad_1.5x1.5mm
TP13, TP14: ALERT; TestPoint_Pad_1.0x1.0mm
U2: OV5640-A71A; BGA71C50P11X11_598X584X81
U4: ORION-B16; U-SkyTraq-ORION-B16

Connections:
1V8 MEASURE: IC7.1 (IN+), R15.1; also elsewhere on the board
3V3 MEASURE: IC6.1 (IN+), R14.1; also elsewhere on the board
+1V5: C42.2, C47.2, J9.1, U2.A9 (DVDD), U2.B5 (DVDD@1), U2.C1 (DVDD@2), U2.D2 (DVDD@3), U2.I11 (DVDD@6), U2.J1 (DVDD@4), U2.J7 (EVDD), U2.K1 (DVDD@5)
+1V8: C25.1, C26.1, C45.2, C48.1, C49.1, IC4.5 (V+), IC6.4 (VS), IC7.2 (IN-), IC7.4 (VS), IC8.4 (ADD0), IC8.5 (V+), IC12.5 (V+), IC13.5 (V+), JP1.2 (B), R7.1, R8.1, R9.1, R10.1, R11.1, R12.1, R15.2, U2.J2 (DOVDD), U2.J3 (DOVDD@1), U2.K2 (DOVDD@2), U2.K3 (DOVDD@3); also elsewhere on the board
+2V8: C40.2, C41.2, C46.2, J8.1, U2.A3 (AVDD), U2.B10 (AVDD@1), U2.C11 (AVDD@2), U2.I10 (PVDD)
+3V3: C24.2, C52.1, C53.1, IC5.14 (VCC), IC6.2 (IN-), R13.1, R14.2, U4.22 (V_BCKP), U4.23 (VCC); also elsewhere on the board
DCMI_D0: U2.K5 (D0/GPIO2); also elsewhere on the board
DCMI_D1: U2.K4 (D1/GPIO3); also elsewhere on the board
DCMI_D2: U2.J5 (D2); also elsewhere on the board
DCMI_D3: U2.H10 (D3); also elsewhere on the board
DCMI_D4: U2.K6 (D4/MDN0); also elsewhere on the board
DCMI_D5: U2.K7 (D5/MDP0); also elsewhere on the board
DCMI_D6: U2.I8 (D6/MCN); also elsewhere on the board
DCMI_D7: U2.I9 (D7/MCP); also elsewhere on the board
DCMI_D8: U2.J9 (D8/MDN1); also elsewhere on the board
DCMI_D9: U2.J10 (D9/MDP1); also elsewhere on the board
DCMI_HSYNC: U2.H2 (HREF); also elsewhere on the board
DCMI_PIXCLK: U2.I1 (PCLK); also elsewhere on the board
DCMI_VSYNC: U2.H1 (VSYNC); also elsewhere on the board
DCMI_XCLK: U2.H11 (XVCLK); also elsewhere on the board
GND: C24.1, C25.2, C26.2, C27.1, C28.1, C29.2, C40.1, C41.1, C42.1, C43.2, C44.2, C45.1, C46.1, C47.1, C48.2, C49.2, C52.2, C53.2, IC4.2 (GND), IC4.4 (ADD0), IC4.7 (EP), IC5.1 (A0), IC5.2 (A1), IC5.7 (GND), IC6.3 (GND), IC6.7 (A0), IC7.3 (GND), IC7.7 (A0), IC8.2 (GND), IC8.7 (EP), IC9.9 (SDO_/_AD0), IC9.11 (FSYNC), IC9.18 (GND), IC9.20 (RESV_2), IC9.25 (EP), IC12.2 (GND), IC12.7 (EP), IC13.2 (GND), IC13.7 (EP), J8.2, J9.2, J12.2 (GND_1), J12.3 (GND_2), U2.A4 (AGND), U2.A5 (DGND), U2.A10 (AGND@1), U2.B1 (DGND@1), U2.B3 (VCMGND), U2.B4 (VCMGND@1), U2.B9 (DGND@2), U2.C2 (DGND@3), U2.D11 (AGND@2), U2.F11 (SGND), U2.G2 (DOGND), U2.I2 (DGND@4), U2.J4 (DOGND@1), U2.J11 (DOGND@2), U2.K8 (EGND), U2.K11 (EGND@1), U4.10 (GND), U4.12 (GND), U4.13 (GND), U4.24 (GND); also elsewhere on the board
I2C1_SCL: IC9.23 (SCL_/_SCLK); also elsewhere on the board
I2C1_SDA: IC9.24 (SDA_/_SDI); also elsewhere on the board
I2C2_SCL: IC5.12 (SCL), J10.4, J10.6; also elsewhere on the board
I2C2_SDA: IC5.13 (SDA), J10.2, J10.8; also elsewhere on the board
I2C4_SCL: U2.G10 (SIOC); also elsewhere on the board
I2C4_SDA: U2.G11 (SIOD); also elsewhere on the board
INTMUX0: R12.2
INTMUX1: IC4.3 (ALERT), IC5.4 (~INT0), IC5.8 (~INT1), IC8.3 (ALERT), IC12.3 (ALERT), IC13.3 (ALERT), R11.2
MPU_1V8: C27.2, C28.2, IC9.8 (VDDIO), IC9.13 (VDD), IC9.22 (NCS), JP1.1 (A)
MPU_INT: IC9.12 (INT1); also elsewhere on the board
unnamed: C29.1, IC9.10 (REGOUT)
unnamed: C43.1, U2.B11 (VN)
unnamed: C44.1, U2.C10 (VH)
unnamed: IC6.8 (ALERT), TP13.1
unnamed: IC7.8 (ALERT), TP14.1
unnamed: J12.1 (SIGNAL), U4.11 (RF_IN)
unnamed: R13.2, TP11.1, U4.8 (RSTN)
unnamed: TP7.1, U2.A2 (VCMSINK), U2.B2 (VCMSINK@1)
unnamed: TP8.1, U2.E1 (STROBE)
unnamed: TP9.1, U2.F2 (FREX)
unnamed: TP12.1, U4.1 (BOOT_SEL)
OV5640_GPIO0: U2.F1 (GPIO0); also elsewhere on the board
OV5640_GPIO1: U2.G1 (GPIO1); also elsewhere on the board
OV5640_PWRDN: U2.D1 (PWDN); also elsewhere on the board
OV5640_RST: U2.E2 (~RESETB); also elsewhere on the board
SCLMUX0: IC5.6 (SC0), IC6.5 (SCL), IC7.5 (SCL), J10.5, R10.2
SCLMUX1: IC4.1 (SCL), IC5.10 (SC1), IC8.1 (SCL), IC12.1 (SCL), IC12.4 (ADD0), IC13.1 (SCL), J10.3, R8.2
SDAMUX0: IC5.5 (SD0), IC6.6 (SDA), IC7.6 (SDA), J10.7, R9.2
SDAMUX1: IC4.6 (SDA), IC5.9 (SD1), IC8.6 (SDA), IC12.6 (SDA), IC13.4 (ADD0), IC13.6 (SDA), J10.1, R7.2
STQ-PPS: U4.3 (1PPS)
SWITCH_INT: IC5.11 (~INT); also elsewhere on the board
SWITCH_RESET: IC5.3 (~RESET), TP10.1; also elsewhere on the board
UART2_RX: U4.21 (RXD); also elsewhere on the board
UART2_TX: U4.20 (TXD); also elsewhere on the board

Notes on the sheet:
ANALOG
Accel, Gyro, Mag, Motion processing Sensor
I2C Adress Selection for ADD0 GND = 0x48 V+ = 0x49 SDA = 0x4A SCL = 0x4B
Tempurature Sensors
I2C address 0x68 when AD0 is GND 0x69 when AD0 is VDD
OV5640 BGA Chip (Optional)
GPS Module
Current Sensors
I2C Switch
CORE

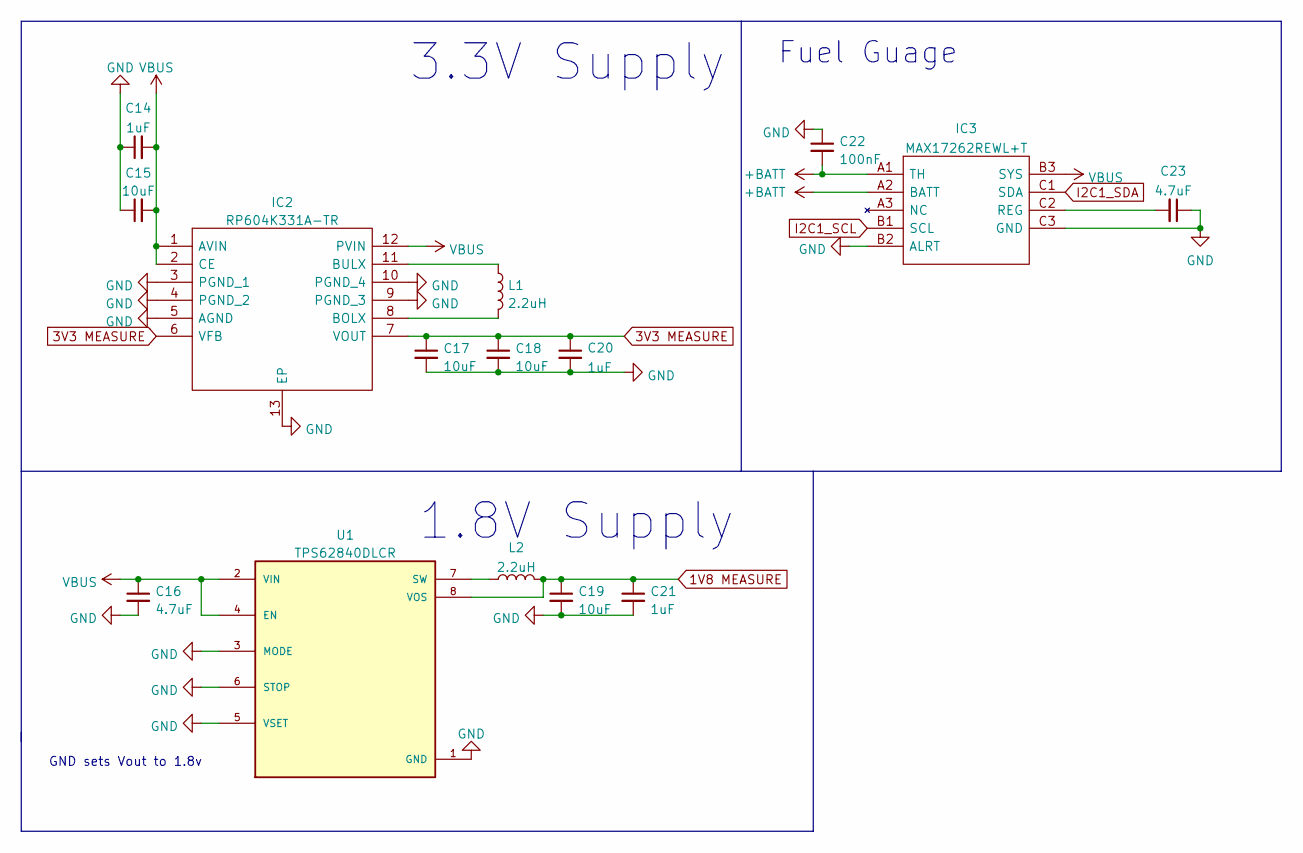
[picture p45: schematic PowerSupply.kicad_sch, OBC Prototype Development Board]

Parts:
C14, C20, C21: 1uF; C_0402_1005Metric
C15, C17, C18, C19: 10uF; C_0402_1005Metric
C16, C23: 4.7uF; C_0402_1005Metric
C22: 100nF; C_0402_1005Metric
IC2: RP604K331A-TR; SON50P270X300X60-13N; Mouser Part Number 848-RP604K331A-TR
IC3: MAX17262REWL+T; BGA9C40P3X3_147X145X69; Mouser Part Number 700-MAX17262REWL+T
L1, L2: 2.2uH; L_1008_2520Metric
U1: TPS62840DLCR; SON50P200X150X100-8N

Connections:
1V8 MEASURE: C19.1, C21.1, L2.2, U1.8 (VOS); also elsewhere on the board
3V3 MEASURE: C17.1, C18.1, C20.1, IC2.6 (VFB), IC2.7 (VOUT); also elsewhere on the board
+BATT: C22.2, IC3.A1 (TH), IC3.A2 (BATT); also elsewhere on the board
GND: C14.1, C15.1, C16.2, C17.2, C18.2, C19.2, C20.2, C21.2, C22.1, C23.1, IC2.3 (PGND_1), IC2.4 (PGND_2), IC2.5 (AGND), IC2.9 (PGND_3), IC2.10 (PGND_4), IC2.13 (EP), IC3.B2 (ALRT), IC3.C3 (GND), U1.1 (GND), U1.3 (MODE), U1.5 (VSET), U1.6 (STOP); also elsewhere on the board
I2C1_SCL: IC3.B1 (SCL); also elsewhere on the board
I2C1_SDA: IC3.C1 (SDA); also elsewhere on the board
unnamed: C23.2, IC3.C2 (REG)
unnamed: IC2.8 (BOLX), L1.2
unnamed: IC2.11 (BULX), L1.1
unnamed: L2.1, U1.7 (SW)
VBUS: C14.2, C15.2, C16.1, IC2.1 (AVIN), IC2.2 (CE), IC2.12 (PVIN), IC3.B3 (SYS), U1.2 (VIN), U1.4 (EN); also elsewhere on the board

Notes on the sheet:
3.3V Supply
1.8V Supply
GND sets Vout to 1.8v
Fuel Guage

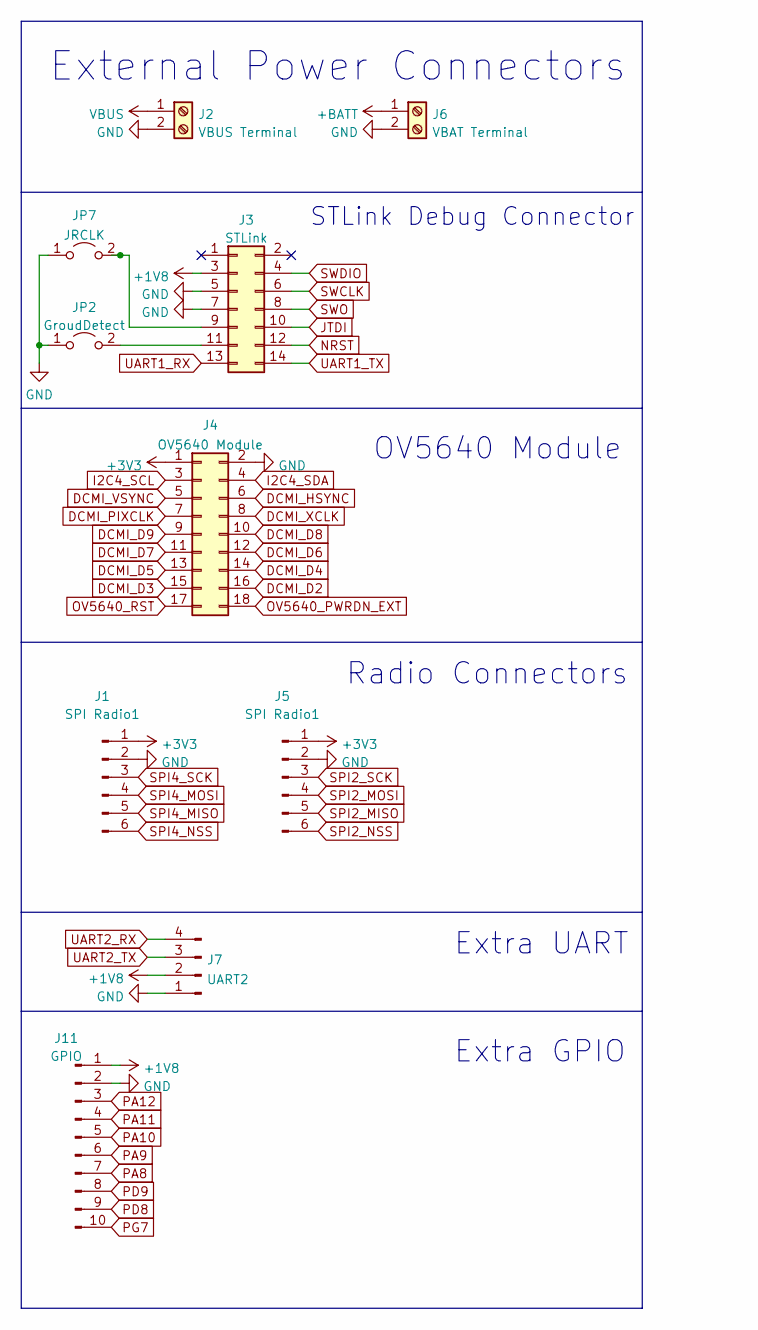
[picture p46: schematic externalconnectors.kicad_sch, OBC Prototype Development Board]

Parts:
J1, J5: SPI Radio1; PinHeader_1x06_P2.54mm_Vertical
J2: VBUS Terminal; TerminalBlock_TE_282834-2_1x02_P2.54mm_Horizontal
J3: STLink; PinHeader_2x07_P1.27mm_Vertical
J4: OV5640 Module; PinHeader_2x09_P2.54mm_Vertical
J6: VBAT Terminal; TerminalBlock_TE_282834-2_1x02_P2.54mm_Horizontal
J7: UART2; PinHeader_1x04_P2.54mm_Vertical
J11: GPIO; PinHeader_1x10_P2.54mm_Vertical
JP2: GroudDetect; PinHeader_1x02_P2.54mm_Vertical
JP7: JRCLK; PinHeader_1x02_P2.54mm_Vertical

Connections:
+1V8: J3.3, J7.2, J11.1; also elsewhere on the board
+3V3: J1.1, J4.1, J5.1; also elsewhere on the board
+BATT: J6.1; also elsewhere on the board
DCMI_D2: J4.16; also elsewhere on the board
DCMI_D3: J4.15; also elsewhere on the board
DCMI_D4: J4.14; also elsewhere on the board
DCMI_D5: J4.13; also elsewhere on the board
DCMI_D6: J4.12; also elsewhere on the board
DCMI_D7: J4.11; also elsewhere on the board
DCMI_D8: J4.10; also elsewhere on the board
DCMI_D9: J4.9; also elsewhere on the board
DCMI_HSYNC: J4.6; also elsewhere on the board
DCMI_PIXCLK: J4.7; also elsewhere on the board
DCMI_VSYNC: J4.5; also elsewhere on the board
DCMI_XCLK: J4.8; also elsewhere on the board
GND: J1.2, J2.2, J3.5, J3.7, J4.2, J5.2, J6.2, J7.1, J11.2, JP2.1 (A), JP7.1 (A); also elsewhere on the board
I2C4_SCL: J4.3; also elsewhere on the board
I2C4_SDA: J4.4; also elsewhere on the board
JTDI: J3.10; also elsewhere on the board
NRST: J3.12; also elsewhere on the board
unnamed: J3.9, JP7.2 (B)
unnamed: J3.11, JP2.2 (B)
OV5640_PWRDN_EXT: J4.18; also elsewhere on the board
OV5640_RST: J4.17; also elsewhere on the board
PA8: J11.7; also elsewhere on the board
PA9: J11.6; also elsewhere on the board
PA10: J11.5; also elsewhere on the board
PA11: J11.4; also elsewhere on the board
PA12: J11.3; also elsewhere on the board
PD8: J11.9; also elsewhere on the board
PD9: J11.8; also elsewhere on the board
PG7: J11.10; also elsewhere on the board
SPI2_MISO: J5.5; also elsewhere on the board
SPI2_MOSI: J5.4; also elsewhere on the board
SPI2_NSS: J5.6; also elsewhere on the board
SPI2_SCK: J5.3; also elsewhere on the board
SPI4_MISO: J1.5; also elsewhere on the board
SPI4_MOSI: J1.4; also elsewhere on the board
SPI4_NSS: J1.6; also elsewhere on the board
SPI4_SCK: J1.3; also elsewhere on the board
SWCLK: J3.6; also elsewhere on the board
SWDIO: J3.4; also elsewhere on the board
SWO: J3.8; also elsewhere on the board
UART1_RX: J3.13; also elsewhere on the board
UART1_TX: J3.14; also elsewhere on the board
UART2_RX: J7.4; also elsewhere on the board
UART2_TX: J7.3; also elsewhere on the board
VBUS: J2.1; also elsewhere on the board

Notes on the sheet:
Extra UART
OV5640 Module
STLink Debug Connector
Radio Connectors
External Power Connectors
Extra GPIO

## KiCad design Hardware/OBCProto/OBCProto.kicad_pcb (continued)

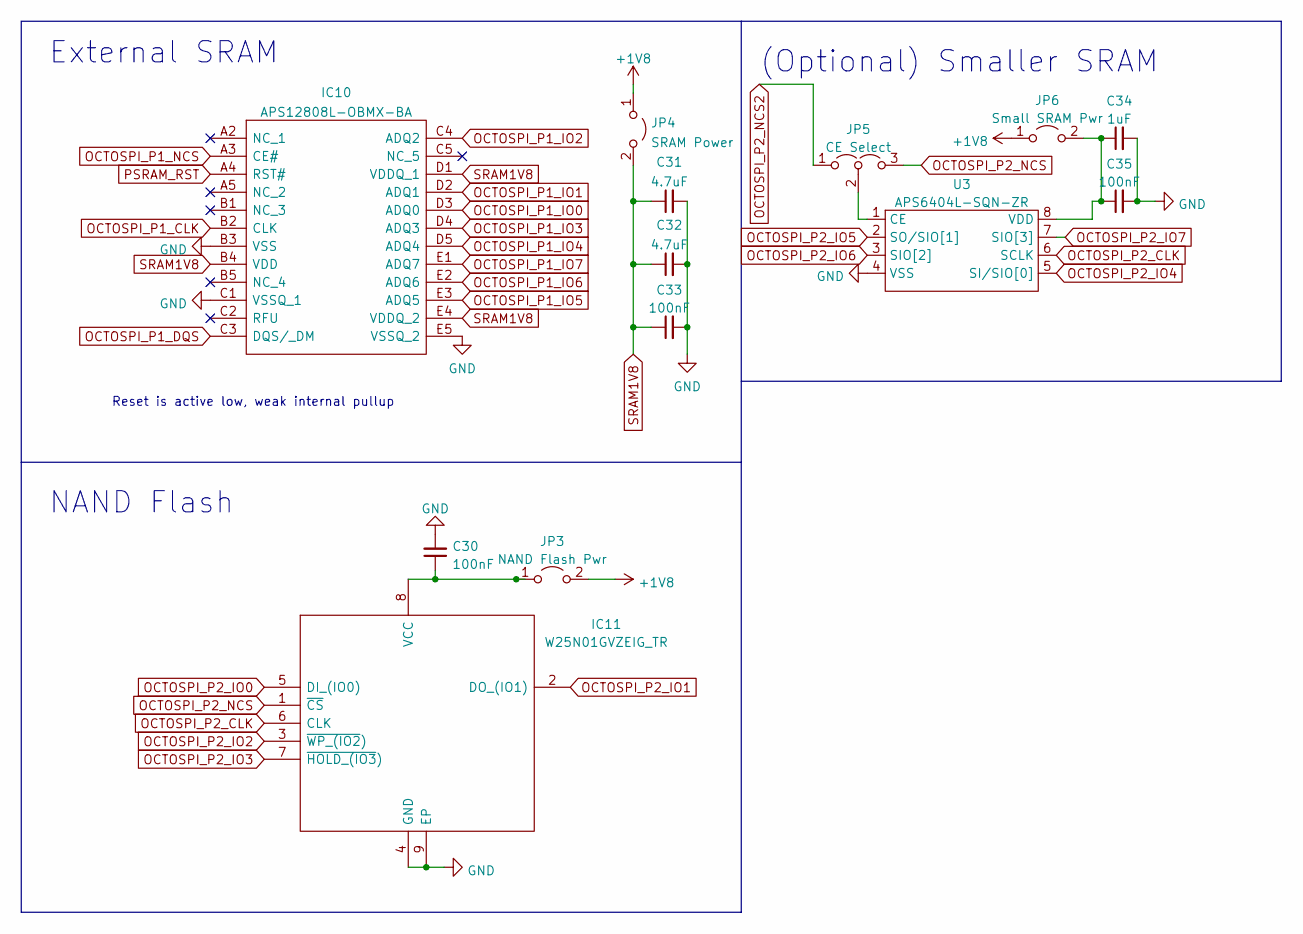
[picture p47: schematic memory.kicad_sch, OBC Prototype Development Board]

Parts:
C30, C33, C35: 100nF; C_0402_1005Metric
C31, C32: 4.7uF; C_0402_1005Metric
C34: 1uF; C_0402_1005Metric
IC10: APS12808L-OBMX-BA; BGA24C100P5X5_600X800X120; Mouser Part Number 878-APS12808L-OBMXBA
IC11: W25N01GVZEIG_TR; SON127P800X600X80-9N-D; Mouser Part Number 454-W25N01GVZEIGTR
JP3: NAND Flash Pwr; PinHeader_1x02_P2.54mm_Vertical
JP4: SRAM Power; PinHeader_1x02_P2.54mm_Vertical
JP5: CE Select; PinHeader_1x03_P2.54mm_Vertical
JP6: Small SRAM Pwr; PinHeader_1x02_P2.54mm_Vertical
U3: APS6404L-SQN-ZR

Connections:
+1V8: JP3.2 (B), JP4.1 (A), JP6.1 (A); also elsewhere on the board
GND: C30.2, C31.2, C32.2, C33.2, C34.2, C35.2, IC10.B3 (VSS), IC10.C1 (VSSQ_1), IC10.E5 (VSSQ_2), IC11.4 (GND), IC11.9 (EP), U3.4 (VSS); also elsewhere on the board
unnamed: C30.1, IC11.8 (VCC), JP3.1 (A)
unnamed: C34.1, C35.1, JP6.2 (B), U3.8 (VDD)
unnamed: JP5.2 (C), U3.1 (CE)
OCTOSPI_P1_CLK: IC10.B2 (CLK); also elsewhere on the board
OCTOSPI_P1_DQS: IC10.C3 (DQS/_DM); also elsewhere on the board
OCTOSPI_P1_IO0: IC10.D3 (ADQ0); also elsewhere on the board
OCTOSPI_P1_IO1: IC10.D2 (ADQ1); also elsewhere on the board
OCTOSPI_P1_IO2: IC10.C4 (ADQ2); also elsewhere on the board
OCTOSPI_P1_IO3: IC10.D4 (ADQ3); also elsewhere on the board
OCTOSPI_P1_IO4: IC10.D5 (ADQ4); also elsewhere on the board
OCTOSPI_P1_IO5: IC10.E3 (ADQ5); also elsewhere on the board
OCTOSPI_P1_IO6: IC10.E2 (ADQ6); also elsewhere on the board
OCTOSPI_P1_IO7: IC10.E1 (ADQ7); also elsewhere on the board
OCTOSPI_P1_NCS: IC10.A3 (CE#); also elsewhere on the board
OCTOSPI_P2_CLK: IC11.6 (CLK), U3.6 (SCLK); also elsewhere on the board
OCTOSPI_P2_IO0: IC11.5 (DI_(IO0)); also elsewhere on the board
OCTOSPI_P2_IO1: IC11.2 (DO_(IO1)); also elsewhere on the board
OCTOSPI_P2_IO2: IC11.3 (~WP_(IO2)); also elsewhere on the board
OCTOSPI_P2_IO3: IC11.7 (~HOLD_(IO3)); also elsewhere on the board
OCTOSPI_P2_IO4: U3.5 (SI/SIO[0]); also elsewhere on the board
OCTOSPI_P2_IO5: U3.2 (SO/SIO[1]); also elsewhere on the board
OCTOSPI_P2_IO6: U3.3 (SIO[2]); also elsewhere on the board
OCTOSPI_P2_NCS: IC11.1 (~CS), JP5.3 (B); also elsewhere on the board
OCTOSPI_P2_NCS2: JP5.1 (A); also elsewhere on the board
PSRAM_RST: IC10.A4 (RST#); also elsewhere on the board
SRAM1V8: C31.1, C32.1, C33.1, IC10.B4 (VDD), IC10.D1 (VDDQ_1), IC10.E4 (VDDQ_2), JP4.2 (B)

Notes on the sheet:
External SRAM
Reset is active low, weak internal pullup
(Optional) Smaller SRAM
NAND Flash

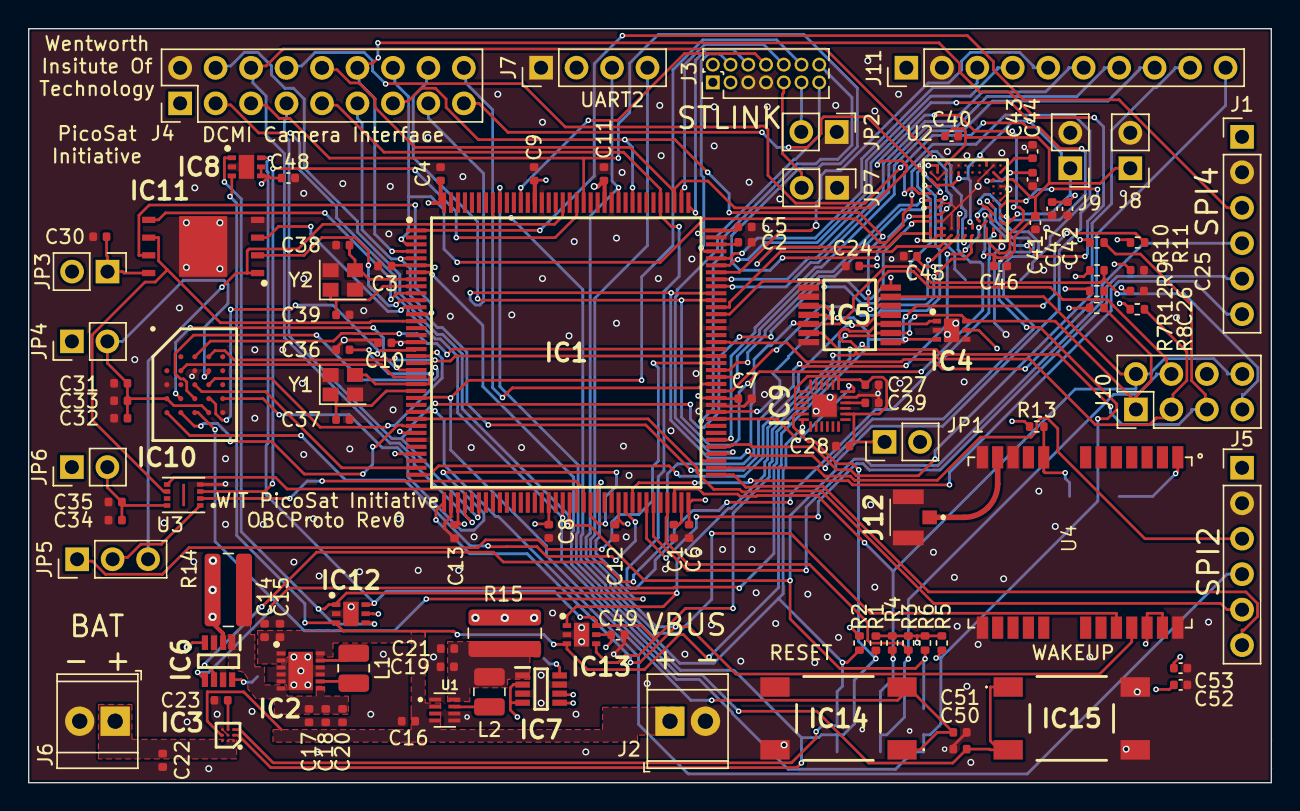
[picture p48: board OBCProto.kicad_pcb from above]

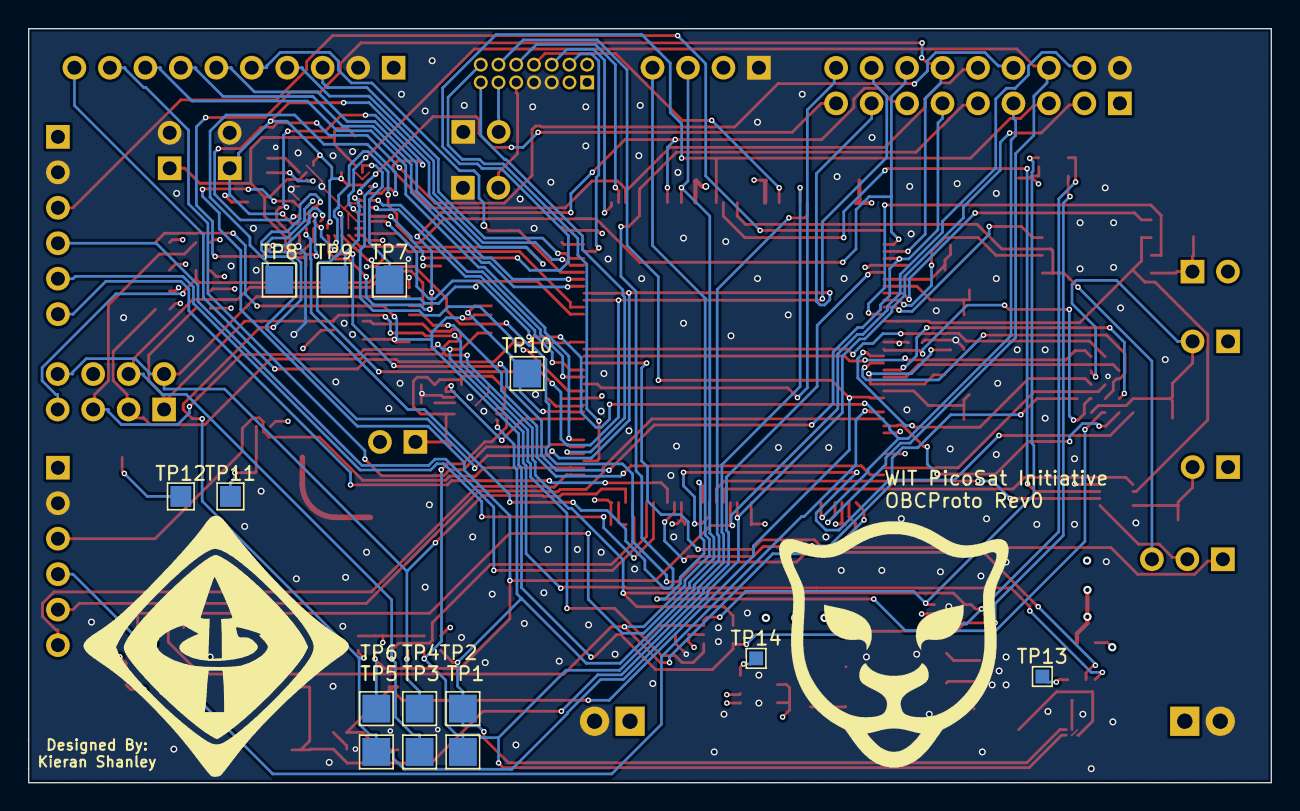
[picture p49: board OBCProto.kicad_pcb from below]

Board: 4 copper layers, 89.0 x 54.0 mm, 124 parts (14 on the bottom side), 118 nets.

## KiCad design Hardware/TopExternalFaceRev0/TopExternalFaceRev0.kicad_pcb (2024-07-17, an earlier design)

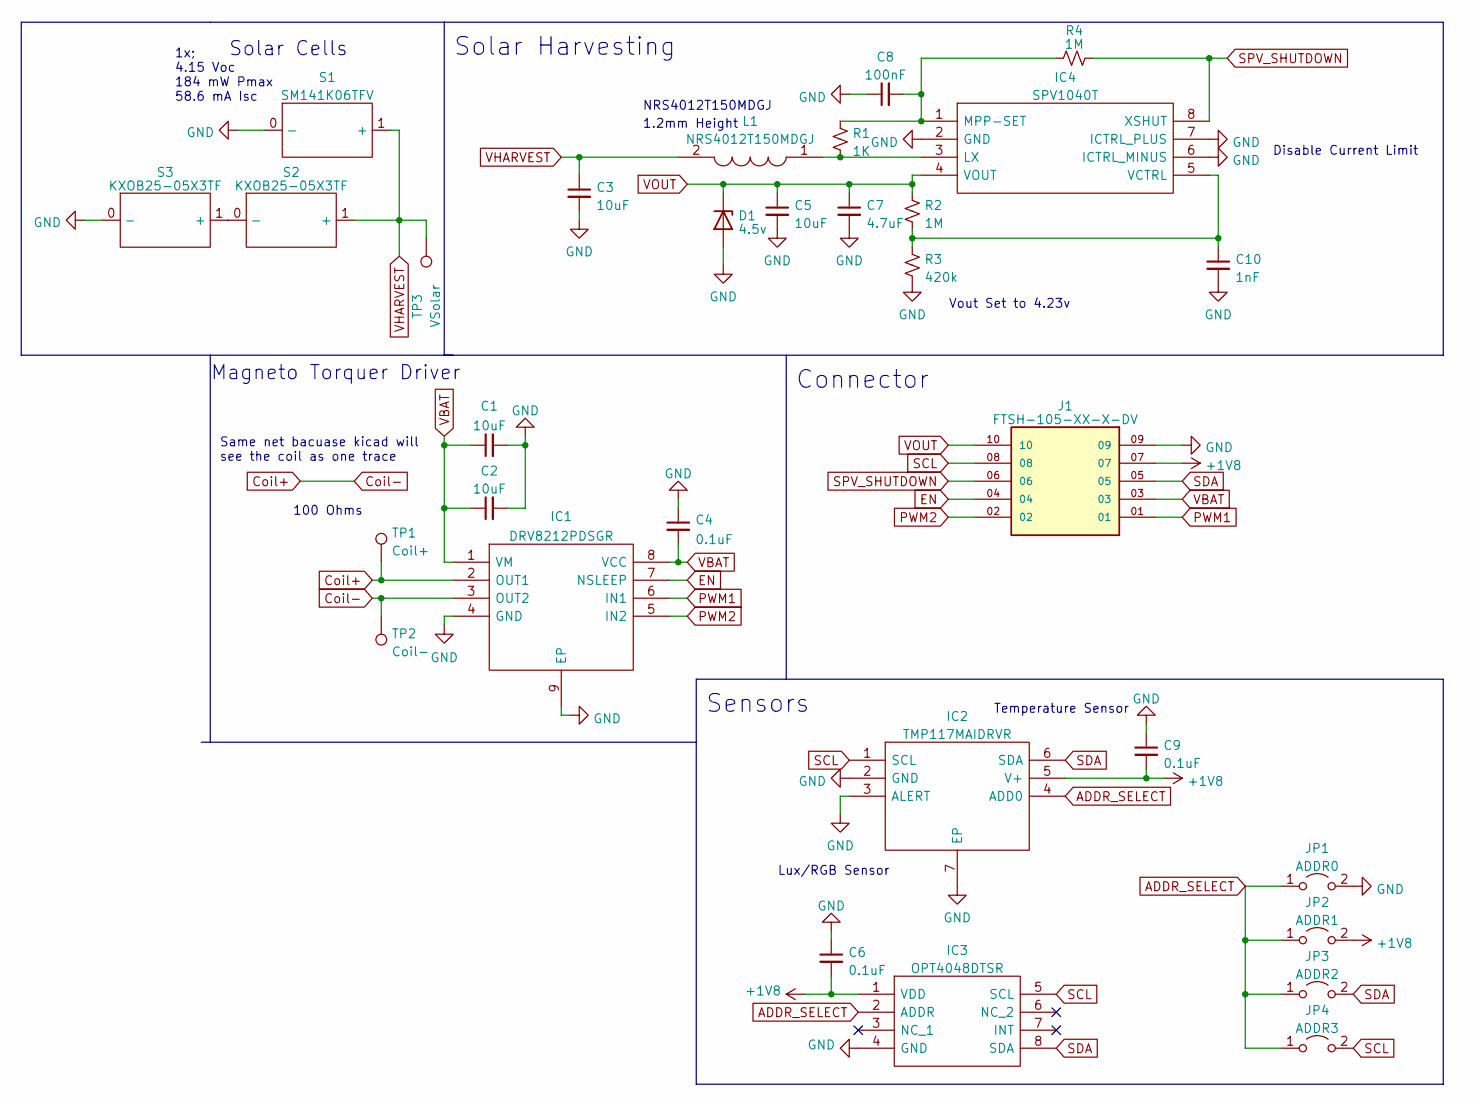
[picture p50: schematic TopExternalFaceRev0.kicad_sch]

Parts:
C1, C2, C3, C5: 10uF; C_0402_1005Metric
C4, C6, C9: 0.1uF; C_0402_1005Metric
C7: 4.7uF; C_0402_1005Metric
C8: 100nF; C_0402_1005Metric
C10: 1nF; C_0402_1005Metric
D1: 4.5v; D_SOD-123
IC1: DRV8212PDSGR; SON50P200X200X80-9N; Mouser Part Number 595-DRV8212PDSGR
IC2: TMP117MAIDRVR; SON65P200X200X80-7N; Mouser Part Number 595-TMP117MAIDRVR
IC3: OPT4048DTSR; SOTFL50P190X60-8N; Mouser Part Number 595-OPT4048DTSR
IC4: SPV1040T; SOP65P640X120-8N; Mouser Part Number 511-SPV1040T
J1: FTSH-105-XX-X-DV; SAMTEC_FTSH-105-XX-X-DV; PARTREV H
JP1: ADDR0; SolderJumper-2_P1.3mm_Open_Pad1.0x1.5mm
JP2: ADDR1; SolderJumper-2_P1.3mm_Open_Pad1.0x1.5mm
JP3: ADDR2; SolderJumper-2_P1.3mm_Open_Pad1.0x1.5mm
JP4: ADDR3; SolderJumper-2_P1.3mm_Open_Pad1.0x1.5mm
L1: NRS4012T150MDGJ; Mouser Part Number 963-NRS4012T150MDGJ
R1: 1K; R_0402_1005Metric
R2, R4: 1M; R_0402_1005Metric
R3: 420k; R_0402_1005Metric
S1: SM141K06TFV
S2, S3: KXOB25-05X3TF
TP1: Coil+; TestPoint_Pad_D2.0mm
TP2: Coil-; TestPoint_Pad_D2.0mm
TP3: VSolar; TestPoint_Pad_1.0x1.0mm

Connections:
+1V8: C6.2, C9.2, IC2.5 (V+), IC3.1 (VDD), J1.07, JP2.2 (B)
ADDR_SELECT: IC2.4 (ADD0), IC3.2 (ADDR), JP1.1 (A), JP2.1 (A), JP3.1 (A), JP4.1 (A)
Coil+: IC1.2 (OUT1), IC1.3 (OUT2), TP1.1, TP2.1
EN: IC1.7 (NSLEEP), J1.04
GND: C1.2, C2.2, C3.2, C4.1, C5.2, C6.1, C7.2, C8.1, C9.1, C10.2, D1.2 (A), IC1.4 (GND), IC1.9 (EP), IC2.2 (GND), IC2.3 (ALERT), IC2.7 (EP), IC3.4 (GND), IC4.2 (GND), IC4.6 (ICTRL_MINUS), IC4.7 (ICTRL_PLUS), J1.09, JP1.2 (B), R3.2, S1.0 (-), S3.0 (-)
unnamed: IC4.3 (LX), L1.1, R1.2
unnamed: C8.2, IC4.1 (MPP-SET), R1.1, R4.1
unnamed: C10.1, IC4.5 (VCTRL), R2.2, R3.1
unnamed: S2.0 (-), S3.1 (+)
PWM1: IC1.6 (IN1), J1.01
PWM2: IC1.5 (IN2), J1.02
SCL: IC2.1 (SCL), IC3.5 (SCL), J1.08, JP4.2 (B)
SDA: IC2.6 (SDA), IC3.8 (SDA), J1.05, JP3.2 (B)
SPV_SHUTDOWN: IC4.8 (XSHUT), J1.06, R4.2
VBAT: C1.1, C2.1, C4.2, IC1.1 (VM), IC1.8 (VCC), J1.03
VHARVEST: C3.1, L1.2, S1.1 (+), S2.1 (+), TP3.1
VOUT: C5.1, C7.1, D1.1 (K), IC4.4 (VOUT), J1.10, R2.1

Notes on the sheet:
Lux/RGB Sensor
Sensors
100 Ohms
Vout Set to 4.23v
Solar Cells
Disable Current Limit
1.2mm Height
Solar Harvesting
NRS4012T150MDGJ
Same net bacuase kicad will see the coil as one trace
Magneto Torquer Driver
Connector
1x; 4.15 Voc 184 mW Pmax 58.6 mA Isc
Temperature Sensor

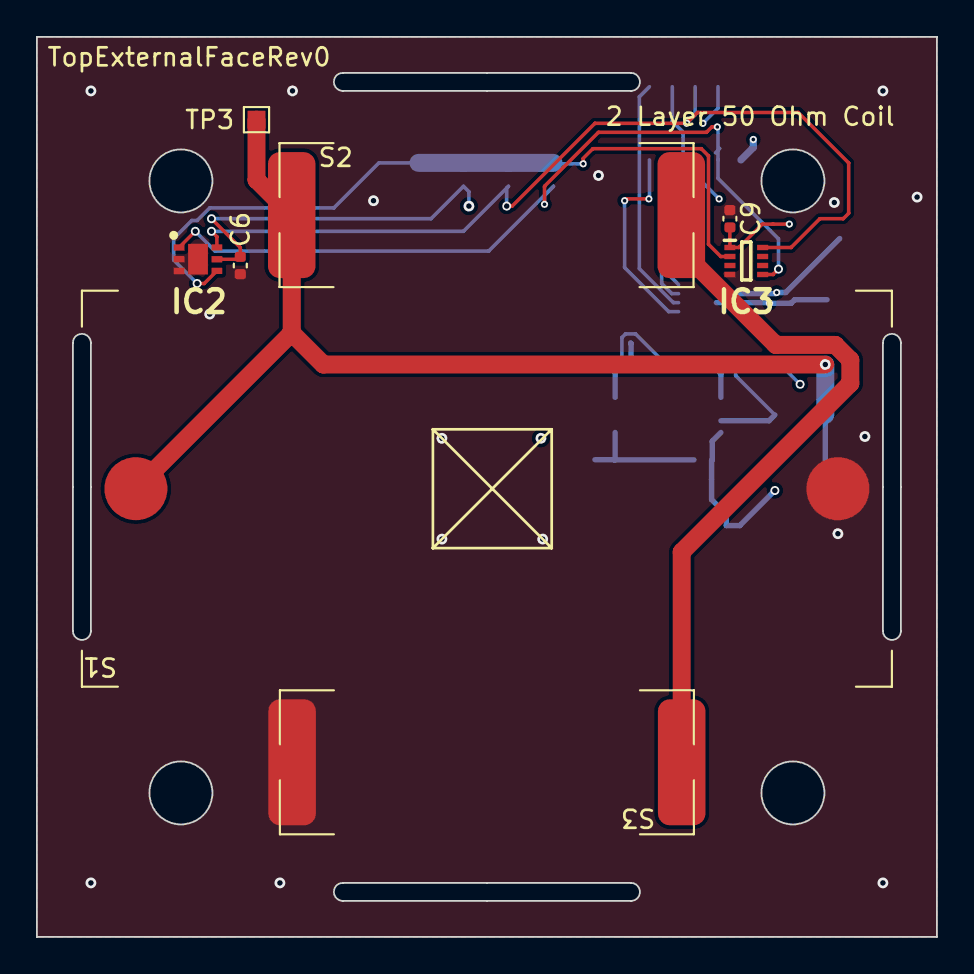
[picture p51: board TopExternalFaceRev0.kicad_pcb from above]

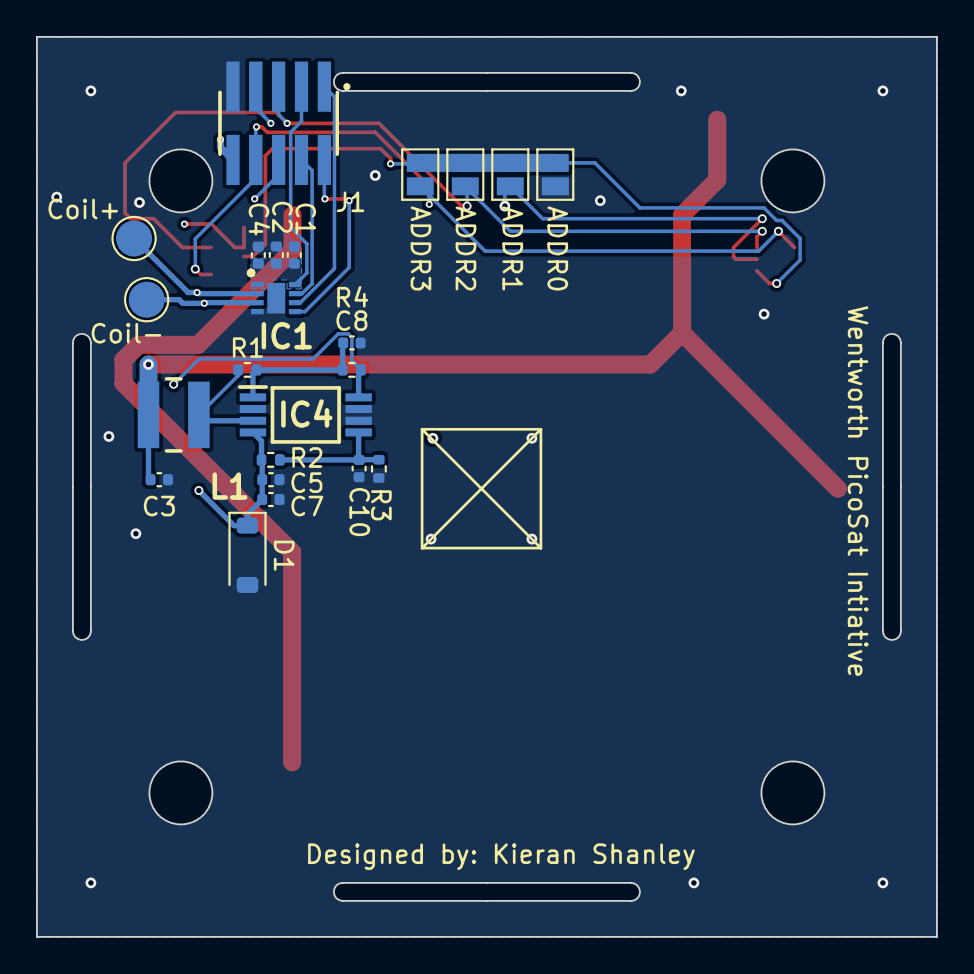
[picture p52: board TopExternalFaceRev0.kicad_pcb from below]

Board: 4 copper layers, 50.0 x 50.0 mm, 31 parts (23 on the bottom side), 17 nets.

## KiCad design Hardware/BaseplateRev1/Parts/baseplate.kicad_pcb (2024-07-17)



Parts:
C5: 4.7uF; C_0402_1005Metric
C6, C9, C10, C11: 10uF; C_0402_1005Metric
C7, C8, C12: 1uF; C_0402_1005Metric
C13, C14: 0.1uF; C_0402_1005Metric
IC1: RP604K331A-TR; SON50P270X300X60-13N; Mouser Part Number 848-RP604K331A-TR
IC2, IC3, IC4: INA236AIDDFR; SOP65P280X110-8N; Manufacturer_Part_Number INA236AIDDFR; Mouser Part Number 595-INA236AIDDFR
IC5: TMP117MAIDRVR; SON65P200X200X80-7N; Mouser Part Number 595-TMP117MAIDRVR
IC6: OPT4048DTSR; SOTFL50P190X60-8N; Mouser Part Number 595-OPT4048DTSR
IC7: TPS62840DLCR; SON50P200X150X100-8N
J1: Conn_Coaxial; U.FL_Molex_MCRF_73412-0110_Vertical
J2, J3: FLE-108-01-XX-DV
J4, J9, J10, J11, J12: FTSH-105-XX-X-DV; SAMTEC_FTSH-105-XX-X-DV; PARTREV H
L1, L2: 2.2uH; L_1008_2520Metric
Q1, Q2: 2N7002; Transistor for baseplate
R1, R2: R_Small_US; R_Axial_DIN0204_L3.6mm_D1.6mm_P7.62mm_Horizontal
R5, R6, R7: 20m; R_1020_2550Metric
SW1, SW2: SW_SPDT; D2FL2A1
U1, U2: antenna

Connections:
1.8V: IC3.2 (IN-), J2.9, J4.07, J9.07, J10.07, J11.07, J12.07, R6.2
1V8 MEASURE: C6.1, C7.1, IC3.1 (IN+), IC7.8 (VOS), L1.2, R6.1
3.3V: IC2.2 (IN-), J2.5, R5.2
3V3 MEASURE: C10.1, C11.1, C12.1, IC1.6 (VFB), IC1.7 (VOUT), IC2.1 (IN+), R5.1
+1V8: C13.2, C14.2, IC2.4 (VS), IC3.4 (VS), IC4.4 (VS), IC5.5 (V+), IC6.1 (VDD)
Battery +: C5.1, C8.2, C9.2, IC1.1 (AVIN), IC1.2 (CE), IC1.12 (PVIN), IC4.2 (IN-), IC7.2 (VIN), IC7.4 (EN), J2.2, J3.13, J4.03, J9.03, J10.03, J11.03, J12.03, Q1.2 (S), Q2.2 (S), R7.2, SW1.1 (A), SW2.1 (A)
DRV ENABLE 1: J2.14, J9.04
DRV ENABLE 2: J2.12, J10.04
DRV ENABLE 3: J2.10, J11.04
DRV ENABLE 4: J2.8, J12.04
DRV ENABLE 5: J2.6, J4.04
GND: C5.2, C6.2, C7.2, C8.1, C9.1, C10.2, C11.2, C12.2, C13.1, C14.1, IC1.3 (PGND_1), IC1.4 (PGND_2), IC1.5 (AGND), IC1.9 (PGND_3), IC1.10 (PGND_4), IC1.13 (EP), IC2.3 (GND), IC2.7 (A0), IC2.8 (ALERT), IC3.3 (GND), IC3.7 (A0), IC3.8 (ALERT), IC4.3 (GND), IC4.7 (A0), IC4.8 (ALERT), IC5.2 (GND), IC5.3 (ALERT), IC5.4 (ADD0), IC5.7 (EP), IC6.2 (ADDR), IC6.4 (GND), IC7.1 (GND), IC7.3 (MODE), IC7.5 (VSET), IC7.6 (STOP), J1.2 (Ext), J2.13, J3.14, J3.15, J3.16, J4.09, J9.09, J10.09, J11.09, J12.09, R1.2, R2.2, U1.1 (RF_IN)
MCU ENABLE 1: J2.3, Q1.1 (G)
MCU ENABLE 2: J2.1, Q2.1 (G)
MPPT ENABLE: J2.4, J4.06, J9.06, J10.06, J11.06, J12.06
unnamed: IC1.8 (BOLX), L2.2
unnamed: IC1.11 (BULX), L2.1
unnamed: IC7.7 (SW), L1.1
unnamed: Q1.3 (D), R1.1
unnamed: Q2.3 (D), R2.1
PWM1(1): J3.10, J9.01
PWM1(2): J3.11, J10.01
PWM1(3): J3.7, J11.01
PWM1(4): J3.3, J12.01
PWM1(5): J2.15, J4.01
PWM2(1): J3.12, J9.02
PWM2(2): J3.9
PWM2(2): J10.02
PWM2(3): J3.5, J11.02
PWM2(4): J3.1, J12.02
PWM2(5): J2.16, J4.02
RF ANTENNA: J1.1 (In), U2.1 (RF_IN)
SCL(1): IC2.5 (SCL), IC3.5 (SCL), IC4.5 (SCL), J3.2, J9.08, J10.08, J11.08, J12.08
SCL(2): IC5.1 (SCL), IC6.5 (SCL), J3.6, J4.08
SDA(1): IC2.6 (SDA), IC3.6 (SDA), IC4.6 (SDA), J3.4, J9.05, J10.05, J11.05, J12.05
SDA(2): IC6.8 (SDA), J3.8, J4.05
SDA(2): IC5.6 (SDA)
VBAT+: J2.7, SW1.2 (B), SW2.2 (B)
VMPPT: IC4.1 (IN+), J2.11, J4.10, J9.10, J10.10, J11.10, J12.10, R7.1

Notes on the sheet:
EXT FACE 2
IN ORDER TO SUPPLY POWER, A BATTERY MUST BE CONNECTED TO VBAT ON KILL SWITCH, AND GROUNDED.
Baseplate to EXT faces conn
Kill switches, normally closed.
Antenna RF connection
Sensors
GND sets Vout to 1.8v
EXT FACE 4
Lux/RGB Sensor
Current Sensors
Temperature Sensor
3.3V Supply
vmppt must join at a node and pass through current senso before becoming vbat
Baseplate to board stack conn
EXT FACE 1
EXT FACE 5 (conn on face 4)
Resistor burning circuit
1.8V Supply
EXT FACE 3



Board: 4 copper layers, 64.0 x 58.0 mm, 38 parts (29 on the bottom side), 36 nets.

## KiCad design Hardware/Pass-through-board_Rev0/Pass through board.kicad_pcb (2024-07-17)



Board: 4 copper layers, 40.0 x 40.0 mm, 53 parts (20 on the bottom side), 26 nets.

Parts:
C1: .1uF; C_0402_1005Metric
C2: .47uF; C_0402_1005Metric
C3: 10uF; R_0603_1608Metric
C3#2, C7, C9, C10: 10uF; C_0402_1005Metric
C4: 22uF; C_0402_1005Metric
C5, C8: 1uF; C_0402_1005Metric
C6, C11: 4.7uF; C_0402_1005Metric
C12: 100nF; C_0402_1005Metric
C13: 1nF; C_0402_1005Metric
D1: 4.5v; D_SOD-123
IC1, IC2, IC6: INA236AIDDFR; SOP65P280X110-8N
IC3: MAX17260SETD+T; SON40P300X300X80-15N
IC4: TPS62840DLCR; SON50P200X150X100-8N
IC5: SPV1040T; SOP65P640X120-8N
IC7: RP602K330G-TR; SON50P270X300X60-13N
IC8: TLV840MADL30DBVRQ1; SOT95P280X145-5N
J1, J2: FLE-108-01-XX-DV; PinHeader_2x08_P1.27mm_Vertical
J3: Conn_01x02_Socket; JST_EH_B2B-EH-A_1x02_P2.50mm_Vertical
J8, J8#2: SLM-108-01-L-D; SAMTEC_SLM-108-01-L-D
JP1: SolderJumper_2_Open; SolderJumper-2_P1.3mm_Open_RoundedPad1.0x1.5mm
L1: 1.0uH; INDPM5650X530N
L2: 2.2uH; L_1008_2520Metric
L3: NRS4012T150MDGJ
Q1: 2N7002; SOT-23
R1, R2, R7: 20m; R_1020_2550Metric
R3: 1K; R_0402_1005Metric
R4, R6: 1M; R_0402_1005Metric
R5: 420k; R_0402_1005Metric
R8: 10m; R_1020_2550Metric
R10, R12: 1M; R_0603_1608Metric
R13: 5k; R_0603_1608Metric
TH1: Thermistor_NTC 10k; JST_EH_B2B-EH-A_1x02_P2.50mm_Vertical
TP1, TP2, TP3, TP4, TP6, TP8: TestPoint_Alt; TestPoint_Pad_1.0x1.0mm
ff: C_0805_2012Metric
gg: C_0805_2012Metric

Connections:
1.8V: IC1.4 (VS), IC2.2 (IN-), IC2.4 (VS), IC6.4 (VS), J1.13, J2.5, Q1.1 (G), R2.2, R13.2, TP3.1
1V8 MEASURE: C7.1, C8.1, IC2.1 (IN+), IC4.8 (VOS), L2.2, R2.1
3.3V: C5.2, IC1.2 (IN-), IC8.2 (VDD), R1.2, TP2.1
3V3 MEASURE: C4.1, IC1.1 (IN+), IC7.6 (VFB), IC7.7 (VOUT), R1.1, ff.1, gg.1
Battery +: C3#2.2, C6.1, IC4.2 (VIN), IC7.1 (AVIN), IC7.12 (PVIN), J1.7, J1.16, R10.1, R12.1, TP1.1
Battery Charge: C1.1, IC3.6 (BATT), IC3.7 (CSN), J3.1, R8.2, TP8.1
CONV_SHUTDOWN: IC4.4 (EN), IC7.2 (CE), IC7.3 (MODE), IC8.1 (~RESET_/_RESET), R10.2
CT: C3.1, IC8.5 (CT)
GND: C1.2, C2.2, C3.2, C3#2.1, C4.2, C5.1, C6.2, C7.2, C8.2, C9.2, C10.2, C11.2, C12.1, C13.2, D1.2 (A), IC1.3 (GND), IC1.7 (A0), IC1.8 (ALERT), IC2.3 (GND), IC2.8 (ALERT), IC3.8 (GND), IC3.9 (CSPL), IC3.15 (EP), IC4.1 (GND), IC4.3 (MODE), IC4.5 (VSET), IC4.6 (STOP), IC5.2 (GND), IC5.6 (ICTRL_MINUS), IC5.7 (ICTRL_PLUS), IC6.3 (GND), IC6.8 (ALERT), IC7.5 (AGND), IC7.9 (PGND_1), IC7.10 (PGND_2), IC7.13 (GROUND), IC8.3 (GND), J1.15, J2.1, J3.2, R5.2, TH1.1, TP4.1, ff.2, gg.2
MPPT ENABLE: IC5.8 (XSHUT), R6.2
unnamed: C2.1, IC3.11 (REG)
unnamed: IC3.1 (TH), TH1.2
unnamed: IC4.7 (SW), L2.1
unnamed: IC5.3 (LX), L3.1, R3.2
unnamed: C12.2, IC5.1 (MPP-SET), R3.1, R6.1
unnamed: C13.1, IC5.5 (VCTRL), R4.2, R5.1
unnamed: IC7.8 (BOLX), L1.2
unnamed: IC7.11 (BULX), L1.1
unnamed: IC8.4 (~MR), Q1.3 (D), R12.2
SAT_REST: Q1.2 (S), R13.1
SCL(1): IC1.5 (SCL), IC2.5 (SCL), IC3.14 (SCL), IC6.5 (SCL), IC6.7 (A0), J1.1
SDA(1): IC1.6 (SDA), IC2.6 (SDA), IC2.7 (A0), IC3.13 (SDA), IC6.6 (SDA), J1.3
VBAT+: J1.14, J2.3, JP1.2 (B)
VMPPT: C10.1, C11.1, D1.1 (K), IC5.4 (VOUT), IC6.1 (IN+), J2.9, R4.1, R7.1
VMPPTCHARGE: IC3.10 (CSPH), IC6.2 (IN-), JP1.1 (A), R7.2, R8.1
Vsolar: C9.1, J2.11, L3.2, TP6.1

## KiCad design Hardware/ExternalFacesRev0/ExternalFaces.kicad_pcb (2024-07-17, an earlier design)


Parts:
C1, C2, C4, C5: 10uF; C_0402_1005Metric
C3, C9, C10: 0.1uF; C_0402_1005Metric
C6: 4.7uF; C_0402_1005Metric
C7: 1nF; C_0402_1005Metric
C8: 100nF; C_0402_1005Metric
D1: 6v; D_SOD-123
IC1: TMP117MAIDRVR; SON65P200X200X80-7N; Mouser Part Number 595-TMP117MAIDRVR
IC2: DRV8212PDSGR; SON50P200X200X80-9N; Mouser Part Number 595-DRV8212PDSGR
IC3: OPT4048DTSR; SOTFL50P190X60-8N; Mouser Part Number 595-OPT4048DTSR
IC4: SPV1040T; SOP65P640X120-8N; Mouser Part Number 511-SPV1040T
J1: Backplane Connector; PinHeader_1x10_P1.00mm_Vertical
JP1: ADDR0; SolderJumper-2_P1.3mm_Open_Pad1.0x1.5mm
JP2: ADDR1; SolderJumper-2_P1.3mm_Open_Pad1.0x1.5mm
JP3: ADDR2; SolderJumper-2_P1.3mm_Open_Pad1.0x1.5mm
JP4: ADDR3; SolderJumper-2_P1.3mm_Open_Pad1.0x1.5mm
L2: NRS4012T150MDGJ; Mouser Part Number 963-NRS4012T150MDGJ
R1: 1K; R_0402_1005Metric
R2: 1M; R_0402_1005Metric
R3: 420k; R_0402_1005Metric
S1, S2: SM141K06TFV
TP1: Coil+; TestPoint_Pad_D2.0mm
TP2: Coil-; TestPoint_Pad_D2.0mm
TP3: VSolar; TestPoint_Pad_1.0x1.0mm

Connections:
+1V8: C9.2, C10.2, IC1.5 (V+), IC3.1 (VDD), J1.3, JP2.2 (B)
ADDR_SELECT: IC1.4 (ADD0), IC3.2 (ADDR), JP1.1 (A), JP2.1 (A), JP3.1 (A), JP4.1 (A)
Coil+: IC2.2 (OUT1), IC2.3 (OUT2), TP1.1, TP2.1
EN: IC2.7 (NSLEEP), J1.8
GND: C1.2, C2.2, C3.1, C4.2, C5.2, C6.2, C7.2, C8.1, C9.1, C10.1, D1.2 (A), IC1.2 (GND), IC1.3 (ALERT), IC1.7 (EP), IC2.4 (GND), IC2.9 (EP), IC3.4 (GND), IC4.2 (GND), IC4.6 (ICTRL_MINUS), IC4.7 (ICTRL_PLUS), J1.5, J1.10, JP1.2 (B), R3.2, S1.0 (-), S2.0 (-)
unnamed: C7.1, IC4.5 (VCTRL), R2.2, R3.1
unnamed: C8.2, IC4.1 (MPP-SET), IC4.8 (XSHUT), R1.1
unnamed: IC4.3 (LX), L2.1, R1.2
PWM1: IC2.6 (IN1), J1.7
PWM2: IC2.5 (IN2), J1.6
SCL: IC1.1 (SCL), IC3.5 (SCL), J1.2, JP4.2 (B)
SDA: IC1.6 (SDA), IC3.8 (SDA), J1.1, JP3.2 (B)
VBAT: C1.1, C2.1, C3.2, IC2.1 (VM), IC2.8 (VCC), J1.9
VHARVEST: C4.1, L2.2, S1.1 (+), S2.1 (+), TP3.1
VOUT: C5.1, C6.1, D1.1 (K), IC4.4 (VOUT), J1.4, R2.1

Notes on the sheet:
Lux/RGB Sensor
4.15 Voc 184 mW Pmax 58.6 mA Isc
1.2mm Height
Solar Harvesting
Magneto Torquer Driver
Vout Set to 4.23v
Solar Cells
Sensors
Temperature Sensor
Disable Current Limit
Connector
100 Ohms
NRS4012T150MDGJ



Board: 8 copper layers, 47.8 x 47.8 mm, 29 parts (20 on the bottom side), 15 nets.

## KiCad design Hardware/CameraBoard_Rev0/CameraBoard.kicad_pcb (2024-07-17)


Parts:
C1, C4, C5, C7, C10, C12: 0.1uF; C_0402_1005Metric
C2, C3, C6, C11: 10uF; C_0402_1005Metric
C8: 100nF; C_0402_1005Metric
C9: 1uF; C_0402_1005Metric
IC1: TPS7A0228PDBVR; SOT95P280X145-5N; Mouser Part Number 595-TPS7A0228PDBVR
IC2: TMP117MAIDRVR; SON65P200X200X80-7N; Mouser Part Number 595-TMP117MAIDRVR
J1: ST4-20-1.50-L-D-P-TR; SAMTEC_ST4-20-1.50-L-D-P-TR; PARTREV J
J2: 2337019-1; 23370191; Mouser Part Number 571-2337019-1
J4: 10051922-2410ELF; 100519222410ELF; Mouser Part Number 649-10051922-2410ELF
R1, R2: 100k; R_0402_1005Metric
R3: 10k; R_0402_1005Metric
TP1: GPS RST; TestPoint_Pad_1.0x1.0mm
TP2: Boot_Sel; TestPoint_Pad_1.0x1.0mm
TP3: Standby; TestPoint_Pad_1.0x1.0mm
TP4: RESET; TestPoint_Pad_1.0x1.0mm
U1: MT9P006I12STCU; LCC70P1000X1000X125-48N
U3: ORION-B16; U-SkyTraq-ORION-B16
Y1: ECS-2520MV-480-CM-TR; ECS2520MV480CMTR; Mouser Part Number 520-2520MV-480-CM-TR

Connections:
+1V8: C5.2, C6.2, C12.1, IC2.5 (V+), J1.01, J1.03, J4.1, J4.14, R1.1, U1.11 (VDD_IO), U1.12 (VDD), U1.39 (VDD_IO), U1.47 (VDD), Y1.4 (VDD)
+2V8: C3.2, C4.2, C10.1, C11.1, IC1.5 (OUT), J4.21, U1.1 (VAA_PIX), U1.23 (VAA), U1.24 (VAA), U1.25 (VDD_PLL), U1.48 (VAA_PIX)
+3.3V: C1.1, C2.1, C8.1, C9.1, IC1.1 (IN), IC1.3 (EN), J1.37, J1.39, R3.1, U3.22 (V_BCKP), U3.23 (VCC)
CAM2_SHUTDOWN: J1.15, J4.17
DOUT0: J1.18, J4.6, U1.33 (DOUT0)
DOUT1: J1.20, J4.4, U1.34 (DOUT1)
DOUT2: J1.22, J4.3, U1.35 (DOUT2)
DOUT3: J1.24, J4.5, U1.36 (DOUT3)
DOUT4: J1.26, J4.7, U1.37 (DOUT4)
DOUT5: J1.28, J4.9, U1.38 (DOUT5)
DOUT6: J1.30, J4.11, U1.40 (DOUT6)
DOUT7: J1.32, J4.13, U1.41 (DOUT7)
DOUT8: J1.34, U1.42 (DOUT8)
DOUT9: J1.36, U1.43 (DOUT9)
DOUT10: J1.38, U1.44 (DOUT10)
DOUT11: J1.40, U1.45 (DOUT11)
EXTCLK: J4.12, U1.31 (EXTCLK), Y1.3 (OUTPUT)
GND: C1.2, C2.2, C3.1, C4.1, C5.1, C6.1, C7.1, C8.2, C9.2, C10.2, C11.2, C12.2, IC1.2 (GND), IC2.2 (GND), IC2.7 (EP), J1.05, J1.06, J1.07, J1.10, J1.19, J1.21, J1.23, J1.25, J1.27, J1.33, J1.35, J2.2 (GND_1), J2.3 (GND_2), J4.2, J4.10, J4.23, J4.MP1, J4.MP2, R2.2, U1.2 (AGND), U1.3 (TEST), U1.6 (RSVD), U1.10 (DGND), U1.13 (SADDR), U1.17 (OE), U1.20 (TEST), U1.21 (TEST), U1.22 (AGND), U1.26 (DGND), U1.46 (DGND), U3.10 (GND), U3.12 (GND), U3.13 (GND), U3.24 (GND), Y1.2 (GND)
GPS_RF: J2.1 (SIGNAL), U3.11 (RF_IN)
GPS_RST: J1.17, R3.2, TP1.1, U3.8 (RSTN)
HSYNC: J1.14, J4.16, U1.8 (LINE_VALID)
unnamed: TP2.1, U3.1 (BOOT_SEL)
PXCLK: J1.08, J4.8, U1.32 (PIXCLK)
RESET: C7.2, J1.02, J4.19, R1.2, TP4.1, U1.16 (~RESET)
SCL: IC2.1 (SCL), J1.09, J4.20, U1.4 (SCLK)
SDA: IC2.4 (ADD0), IC2.6 (SDA), J1.11, J4.22, U1.5 (SDATA)
STANDBY: J1.13, R2.1, TP3.1, U1.14 (~STANDBY), Y1.1 (TRI-STATE)
STQ-PPS: U3.3 (1PPS)
STROBE: J1.16, J4.24, U1.9 (STROBE)
TRIGGER: J1.04, U1.15 (TRIGGER)
UART2_RX: J1.29, U3.21 (RXD)
UART2_TX: J1.31, U3.20 (TXD)
VSYNC: J1.12, J4.18, U1.7 (FRAME_VALID)

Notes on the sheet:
(This oscillator will clock both cameras)
2.8v Supply for Analog Core
OBC Connector
+-50 ppm
GPS Module
Temperature Sensor
48 Mhz Clock
Wide Angle Camera Ribbon Connector
200mA max 25 nA Iq
(OV5640 has internal 1.5v regulator)
Image Sensor



Board: 4 copper layers, 35.0 x 39.0 mm, 27 parts (18 on the bottom side), 32 nets.

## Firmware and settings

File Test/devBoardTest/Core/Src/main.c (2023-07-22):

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
/* Includes ------------------------------------------------------------------*/
#include "main.h"
#include "dcmi.h"
#include "i2c.h"
#include "octospi.h"
#include "usart.h"
#include "gpio.h"

/* USER CODE BEGIN Includes */
#include "log.h"
#include "string.h"
#include "stdbool.h"
#include "INA236.h"
#include "PCA9543.h"
#include "TMP117.h"
#include "aps6408.h"
#include "aps6408_conf.h"
#include "W25Nxx.h"
/* USER CODE END Includes */


/* USER CODE BEGIN PV */
uint8_t aTxBuffer[] = " **OCTOSPI/Octal-spi PSRAM Memory-mapped communication example** **OCTOSPI/Octal-spi PSRAM Memory-mapped communication example** **OCTOSPI/Octal-spi PSRAM Memory-mapped communication example** **OCTOSPI/Octal-spi PSRAM Memory-mapped communication example**";
uint8_t aRxBuffer[512];
/* USER CODE END PV */

void SystemClock_Config(void);
void PeriphCommonClock_Config(void);
/* USER CODE BEGIN PFP */
void Configure_APMemory(void);
static void test_NAND(void);
static void test_PSRAM(void);
/* USER CODE END PFP */

/* USER CODE BEGIN 0 */
INA236_dev INA33Bus;
INA236_dev INA18Bus;
TMP117_dev temp_A;
PCA9543_dev i2c_switch;
W25Nxx_dev W25N;
/* USER CODE END 0 */

/**
  * @brief  The application entry point.
  * @retval int
  */
int main(void)
{
  /* Enable I-Cache---------------------------------------------------------*/
  SCB_EnableICache();

  /* Enable D-Cache---------------------------------------------------------*/
  SCB_EnableDCache();

  /* MCU Configuration--------------------------------------------------------*/

  /* Reset of all peripherals, Initializes the Flash interface and the Systick. */
  HAL_Init();

  /* Configure the system clock */
  SystemClock_Config();

/* Configure the peripherals common clocks */
  PeriphCommonClock_Config();

  /* USER CODE BEGIN SysInit */
  HAL_GPIO_WritePin(GPIOG, GPIO_PIN_5, GPIO_PIN_RESET); //Memory reset
  HAL_GPIO_WritePin(GPIOG, GPIO_PIN_6, GPIO_PIN_SET);
  /* USER CODE END SysInit */

  /* Initialize all configured peripherals */
  MX_GPIO_Init();
  MX_USART1_UART_Init();
  MX_DCMI_Init();
  MX_I2C1_Init();
  MX_I2C2_Init();
  MX_OCTOSPI1_Init();
  MX_OCTOSPI2_Init();
  /* USER CODE BEGIN 2 */


  log_info("Main Init");

  //test_PSRAM();
  test_NAND();

  /* USER CODE END 2 */

  /* Infinite loop */
  /* USER CODE BEGIN WHILE */
  INA236_setup(&INA33Bus, &i2c_bus_2, INA236_ADDR_1);
  INA236_setup(&INA18Bus, &i2c_bus_2, INA236_ADDR_1);
  PCA9543_setup(&i2c_switch, &i2c_bus_2, PCA9543_ADDR_1);
  TMP117_setup(&temp_A, &i2c_bus_2, TMP117_ADDR_1);

  if (PCA9543_set_channel(&i2c_switch, PCA9543_CHANNEL_1) != HAL_OK)
  {
	  log_error("Unable to set i2c switch channel");
  }

  /*
  if (HAL_I2C_IsDeviceReady(&hi2c2, PCA9543_ADDR_1, 2, 1000) != HAL_OK)
  {
	  log_error("Unable to communicate with i2c switch");
  } */

  if (HAL_I2C_IsDeviceReady(&hi2c2, TMP117_ADDR_1 << 1, 2, 1000) != HAL_OK)
  {
	  log_error("Unable to communicate with TMP117_A");
  }
  else {
	  log_info("TMP117_A Ready");
  }

  if (HAL_I2C_IsDeviceReady(&hi2c1, 0b11010000, 2, 1000) != HAL_OK)
  {
	  log_error("Unable to communicate with ICM-20948");
  }
  else {
	  log_info("ICM-20948 Ready");
  }

  while (1)
  {

    /* USER CODE END WHILE */

    /* USER CODE BEGIN 3 */
	float temperature_A = 0;
	if (TMP117_read_temperature(&temp_A, &temperature_A) == HAL_OK) {
		log_info("Temperature A:%f", temperature_A);
	}
	else {
		log_error("Unable to get temp A");
	}

	/*
	float voltage = 0;
	if (INA236_get_bus_voltage(&INA18Bus, &voltage) == HAL_OK) {
	  log_info("1.8v Bus Voltage:%f", voltage);
	}
	else {
	  log_error("Error getting 1.8v bus voltage");
	}
	*/



	HAL_Delay(5000);

  }
  /* USER CODE END 3 */
}

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
/* USER CODE BEGIN 4 */

static void test_NAND(void)
{
	W25N_setup(&W25N, &hospi2, 0);

	uint32_t nand_id = 0;
	uint8_t statReg = 0;
	if (W25N_ReadJEDECID(&W25N, &nand_id) == W25N_OK) {
	  log_info("W25N ID: %X", nand_id);
	}
	else {
	  log_error("Unable to read from W25N");
	}
	W25N_Write_Enable(&W25N);

	W25N_Read_Status_Reg(&W25N, W25N_STATUS_REG, &statReg);
	log_info("W25N status: %X", statReg);
	W25N_Read_Status_Reg(&W25N, W25N_CONFIG_REG, &statReg);
	log_info("W25N config: %X", statReg);
	W25N_Read_Status_Reg(&W25N, W25N_PROTECTION_REG, &statReg);
	log_info("W25N protection: %X", statReg);
	W25N_Write_Status_Reg(&W25N, W25N_PROTECTION_REG, 0x00); //Disable memory protection
	W25N_Write_Status_Reg(&W25N, W25N_CONFIG_REG, 0x18); //Enable ECC and buffer

	W25N_Block_Erase(&W25N, 0x0026);
	W25N_Read_Status_Reg(&W25N, W25N_STATUS_REG, &statReg);
	log_info("W25N status: %X", statReg);
	W25N_Read_Status_Reg(&W25N, W25N_PROTECTION_REG, &statReg);
	log_info("W25N protection: %X", statReg);
	W25N_Wait_Until_Not_Busy(&W25N, 30000);

	memset(aRxBuffer, 0xff, 512);

	W25N_Write_Enable(&W25N); //Must be called before Data load

	if (W25N_Load_Data_Quad(&W25N, 0x00, aTxBuffer, 256) != W25N_OK) {
	  log_error("W25N Unable to load data");
	}

	W25N_Program_Execute(&W25N, 0x0026);
	W25N_Read_Status_Reg(&W25N, W25N_STATUS_REG, &statReg);
	log_info("W25N status after execute: %X", statReg);
	W25N_Wait_Until_Not_Busy(&W25N, 30000);

	W25N_Read_Status_Reg(&W25N, W25N_STATUS_REG, &statReg);
	log_info("W25N status after execute done: %X", statReg);
	W25N_Page_Data_Read(&W25N, 0x0026);
	W25N_Read_Status_Reg(&W25N, W25N_STATUS_REG, &statReg);
	log_info("W25N status after page load: %X", statReg);
	W25N_Wait_Until_Not_Busy(&W25N, 30000);

	W25N_Read_Status_Reg(&W25N, W25N_STATUS_REG, &statReg);
	log_info("W25N status after page load done: %X", statReg);
	if (W25N_Read_Output_Quad(&W25N, 0x00, aRxBuffer, 256) != W25N_OK) {
	  log_error("W25N unable to read output");
	}

	if (aRxBuffer[0] == aTxBuffer[0]) {
	  log_info("----W25N R/W Success----");
	}
	else {
	  log_error("W25N R/W Failure");
	}
}

static void test_PSRAM(void)
{
	__HAL_OSPI_DISABLE(&hospi1);
	HAL_Delay(100);
	CLEAR_BIT(hospi1.Instance->DCR1, OCTOSPI_DCR1_FRCK);
	__HAL_OSPI_ENABLE(&hospi1);
	HAL_GPIO_WritePin(GPIOG, GPIO_PIN_5, GPIO_PIN_SET); //Memory reset pin HIGH
	HAL_GPIO_WritePin(GPIOG, GPIO_PIN_6, GPIO_PIN_RESET);

	if (APS6408_Write(&hospi1, aTxBuffer, 0x00, 4, DUMMY_CLOCK_CYCLES_WRITE, APS6408_MR8_BL_32_BYTES) != HAL_OK) {
	  log_error("Unable to write to APS6408");
	}
	uint32_t testData = 0;
	if (APS6408_Read(&hospi1, (uint8_t *)&testData, 0x00, 4, DUMMY_CLOCK_CYCLES_READ, APS6408_MR8_BL_32_BYTES) != HAL_OK) {
	  log_error("Unable to write to APS6408");
	}

	if (testData != *((uint32_t *)aTxBuffer)) {
	  log_error("APS6048 Read/Write Fail");
	}
	else {
	  log_info("APS6048 Read/Write Success");
	}


	if (APS6408_EnableMemoryMappedMode(&hospi1, APS6408_READ_LATENCY_5, DUMMY_CLOCK_CYCLES_WRITE, APS6408_MR8_BL_32_BYTES) != HAL_OK)
	{
	  log_error("Unable to start APS6408 memory mapped mode");
	}

	__IO uint8_t *mem_addr;
	uint32_t address = 0;
	uint16_t index1;/*index1 counter of bytes used when reading/writing 256 bytes buffer */
	uint16_t index2;/*index2 counter of 256 bytes buffer used */
	bool noErrors = true;
	mem_addr = (__IO uint8_t *)(OCTOSPI1_BASE + address);
	//Writing 1Mbyte (256Byte BUFFERSIZE x 4096 times)
	for (index2 = 0; index2 < EXTENDEDBUFFERSIZE/BUFFERSIZE; index2++)
	{
		for (index1 = 0; index1 < BUFFERSIZE; index1++)
		{
			*mem_addr = aTxBuffer[index1];
			mem_addr++;
		}
	}
	//----------------------------------------------------------------------
	//Reading Sequence of 1Mbyte
	mem_addr = (__IO uint8_t *)(OCTOSPI1_BASE + address);
	//Reading 1Mbyte (256Byte BUFFERSIZE x 4096 times)
	for (index2 = 0; index2 < EXTENDEDBUFFERSIZE/BUFFERSIZE; index2++) {
		for (index1 = 0; index1 < BUFFERSIZE; index1++)
		{
			uint8_t data = *mem_addr;
			if (data != aTxBuffer[index1])
			{
				//if data read is corrupted we can toggle a led here: example blue led
				//log_error("Data Corrupt, %d != %d", data, aTxBuffer[index1]);
				noErrors = false;
			}
				mem_addr++;
		}
	}

	if (noErrors) {
		log_info("PSRAM data transfer success");
	}
	else {
		log_info("PSRAM data transfer failure");
	}
}

void Configure_APMemory(void)
{
  /* MR0 register for read and write */
  uint8_t regW_MR0[2]={0x24,0x0D}; /* To configure AP memory Latency Type and drive Strength */
  uint8_t regR_MR0[2]={0};

  /* MR8 register for read and write */
  uint8_t regW_MR8[2]={0x0B,0x08}; /* To configure AP memory Burst Type */
  uint8_t regR_MR8[2]={0};

  /*Read Latency */
  uint8_t latency=6;

  /* Configure Read Latency and drive Strength */
  if (APS6408_WriteReg(&hospi1, APS6408_MR0_ADDRESS, regW_MR0[0]) != HAL_OK)
  {
    Error_Handler();
  }

  /* Check MR0 configuration */
  if (APS6408_ReadReg(&hospi1, APS6408_MR0_ADDRESS, regR_MR0, latency ) != HAL_OK)
  {
    Error_Handler();
  }

    /* Check MR0 configuration */
  if (regR_MR0 [0] != regW_MR0 [0])
  {
	  log_error("MR0 Set failed");
  }

  /* Configure Burst Length */
  if (APS6408_WriteReg(&hospi1, APS6408_MR8_ADDRESS, regW_MR8[0]) != HAL_OK)
  {
    Error_Handler();
  }

  /* Check MR8 configuration */
  if (APS6408_ReadReg(&hospi1, APS6408_MR8_ADDRESS, regR_MR8, 6) != HAL_OK)
  {
    Error_Handler();
  }

  if (regR_MR8[0] != regW_MR8[0])
  {
	  log_error("MR8 Set Failed");
  }
}
/* USER CODE END 4 */
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


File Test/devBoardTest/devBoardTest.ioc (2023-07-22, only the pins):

Mcu.UserName=STM32H723ZGTx
PA1.Signal=OCTOSPIM_P1_DQS
PA2.Signal=GPIO_Input
PA4.Signal=DCMI_HSYNC
PA6.Signal=DCMI_PIXCLK
PB10.Signal=I2C2_SCL
PB11.Signal=I2C2_SDA
PB13.Signal=DCMI_D2
PB14.Signal=USART1_TX
PB15.Signal=USART1_RX
PB6.Signal=I2C1_SCL
PB7.Signal=I2C1_SDA
PC10.Signal=DCMI_D8
PC12.Signal=DCMI_D9
PC3_C.Signal=OCTOSPIM_P1_IO6
PC6.Signal=DCMI_D0
PC7.Signal=DCMI_D1
PC9.Signal=DCMI_D3
PD13.Signal=GPIO_Output
PD3.Signal=DCMI_D5
PE10.Signal=OCTOSPIM_P1_IO7
PE4.Signal=DCMI_D4
PE5.Signal=DCMI_D6
PE6.Signal=DCMI_D7
PE7.Signal=OCTOSPIM_P1_IO4
PE8.Signal=OCTOSPIM_P1_IO5
PF0.Signal=OCTOSPIM_P2_IO0
PF1.Signal=OCTOSPIM_P2_IO1
PF10.Signal=OCTOSPIM_P1_CLK
PF2.Signal=OCTOSPIM_P2_IO2
PF3.Signal=OCTOSPIM_P2_IO3
PF4.Signal=OCTOSPIM_P2_CLK
PF6.Signal=OCTOSPIM_P1_IO3
PF7.Signal=OCTOSPIM_P1_IO2
PF8.Signal=OCTOSPIM_P1_IO0
PF9.Signal=OCTOSPIM_P1_IO1
PG12.Signal=OCTOSPIM_P2_NCS
PG5.Signal=GPIO_Output
PG6.Signal=OCTOSPIM_P1_NCS
PG9.Signal=DCMI_VSYNC

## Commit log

2023-01-19 Add OV5640 test program
    This program will use DCMI to grab a image from a attached OV5640 and place it into internal memory.
2023-03-13 New test project
    This project will test I2C comms with the INA219 and MAX17048
2023-07-22 clock changes
    fixed clock to use hsi again
    [devBoardTest.ioc, i2c.c, main.c]
2024-03-23 Overview for readme
    Provide a brief overview of the project and hardware for the landing page.
2024-03-23 Documentation for camera system
2024-07-17 Add Hardware
    Add KiCad PCB designs to version control
    [10051922-2410ELF.stp, 2337019-1.stp, APS12808L-OBMX-BA.stp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]

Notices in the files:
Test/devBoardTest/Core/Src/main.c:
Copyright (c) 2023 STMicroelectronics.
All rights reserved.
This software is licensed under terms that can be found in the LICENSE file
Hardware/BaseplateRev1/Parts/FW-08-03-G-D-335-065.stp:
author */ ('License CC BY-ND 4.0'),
